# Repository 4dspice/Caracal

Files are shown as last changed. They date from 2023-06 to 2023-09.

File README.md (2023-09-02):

# Caracal

/!\ This printer is still relatively new please make sure to report any problems in  https://github.com/suslemon/Caracal/issues/1 

A fast, minimalist and modular CoreXY 3D printer that's easy to build and source parts for. All parts designed to be printed without supports. It uses 2020 extrusions and Nema 17 stepper motors. The BOM is kept as tame as possible and avoids the use of difficult to find parts. Some parts can be salvaged from other printers like an Ender 3 to further minimise costs. The printer can easily be enclosed if built using blind joints as all sides are completely flush without brackets.

Caracal was designed with modding and remixing in mind so the build is truly yours.

I printed all my parts with 0.2mm layer height, 0.4mm walls, 4 walls, 4 tops/bottoms, 30% infill (cubic) in eSun ABS+ (should be perfectly fine in PLA for non-enclosed builds) 

BOM https://docs.google.com/spreadsheets/d/1f__scBLHZBergLk1_uNWVnCNQPU6N8hWUedBBvM0iNw/edit#gid=0

YouTube Channel: https://youtube.com/@4dspice

Community Discord: https://discord.gg/pxpvCewKF5 



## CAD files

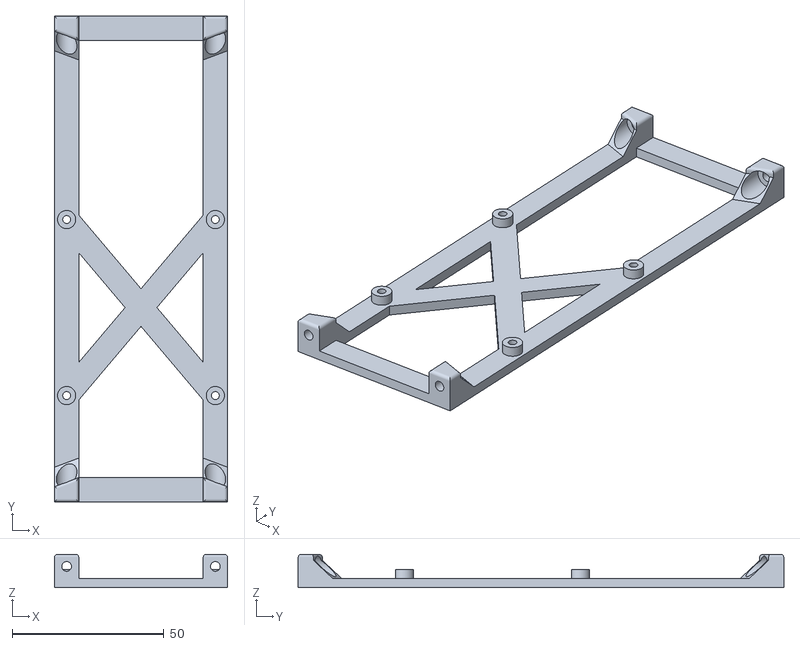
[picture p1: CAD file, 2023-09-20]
STLs/Frame/Raspberry Pi Model B Mount.stl
57.0 x 160.0 x 11.0

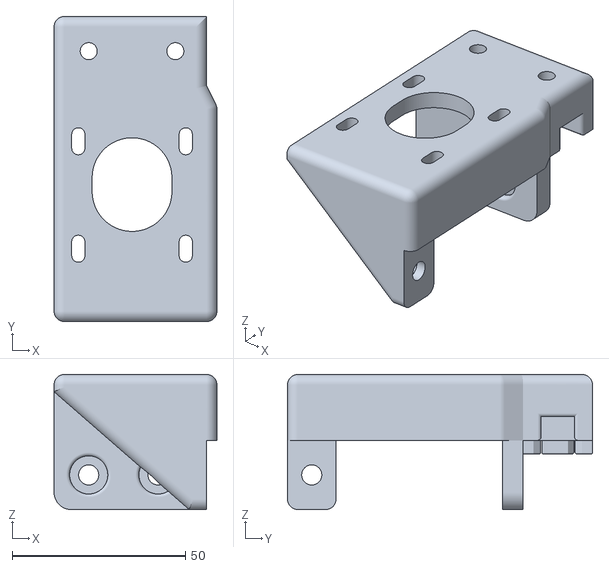
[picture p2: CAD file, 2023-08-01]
STLs/Gantry/Motor Mount - B.stl
47.0 x 88.0 x 39.0

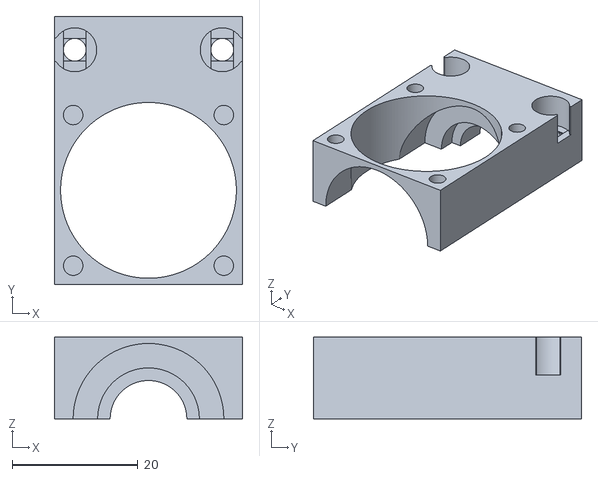
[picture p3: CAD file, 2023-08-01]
STLs/Superfang Toolhead/V6 Hotend Fan Shroud.stl
30.0 x 42.7 x 13.0

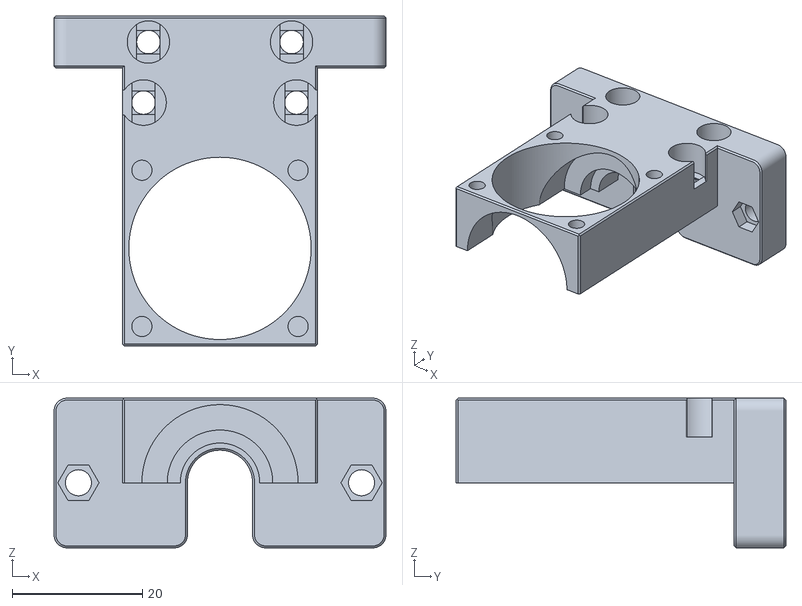
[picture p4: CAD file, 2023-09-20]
STLs/Toolhead/V6 Sherpa Mini Fan Shroud - Direct Drive.stl
51.0 x 50.7 x 23.0

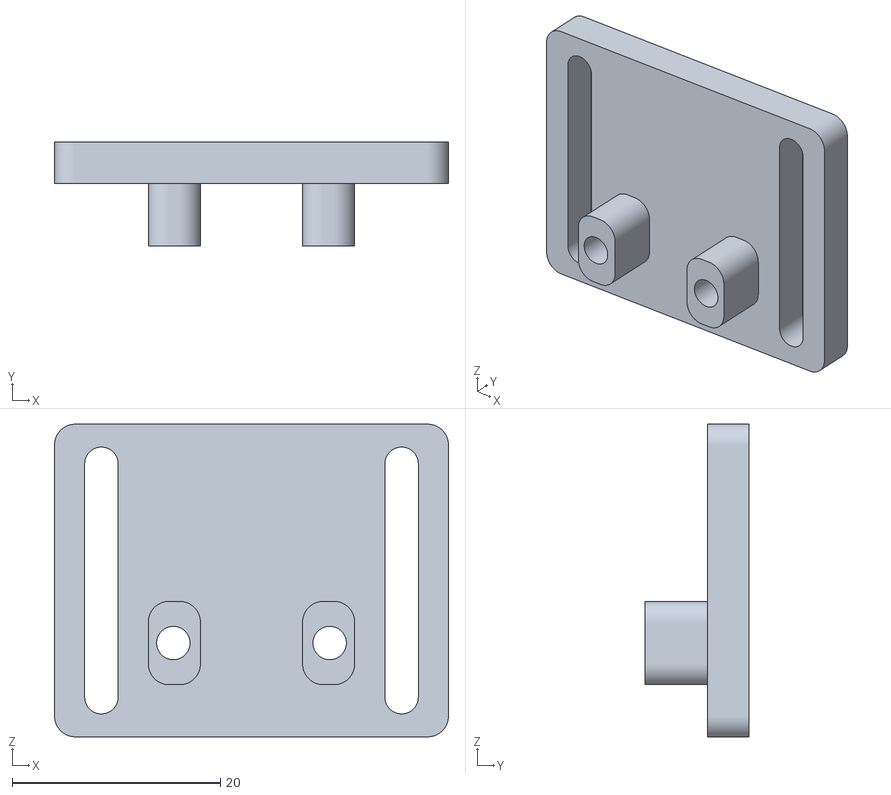
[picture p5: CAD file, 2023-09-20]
STLs/Z Assembly/Endstop Mount Creality Style.stl
37.8 x 10.0 x 30.0

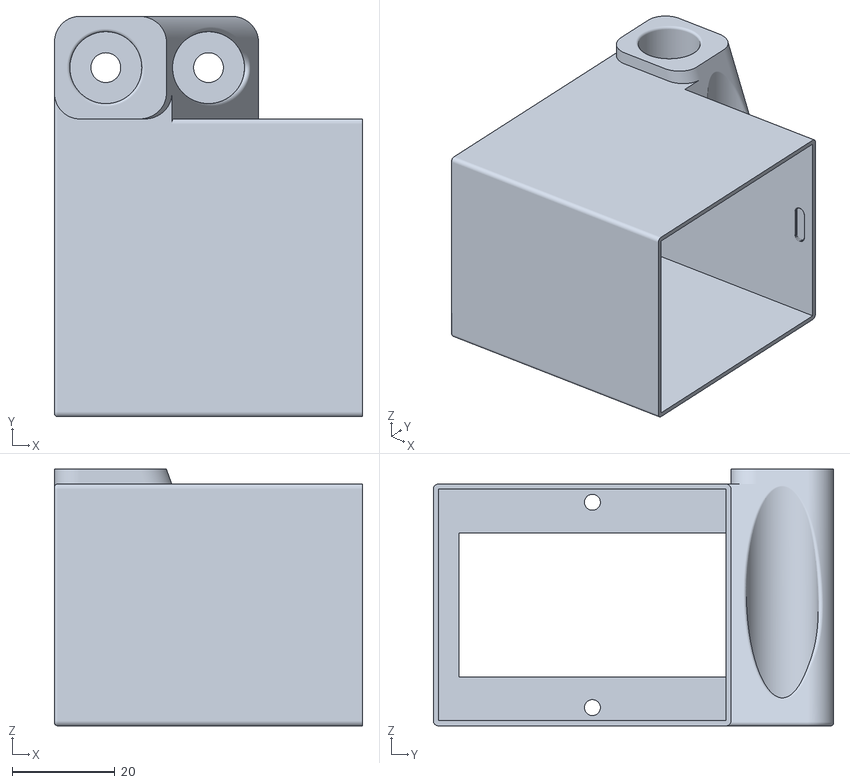
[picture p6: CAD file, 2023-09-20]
STLs/Frame/Foot Power Socket.stl
60.0 x 78.0 x 50.0

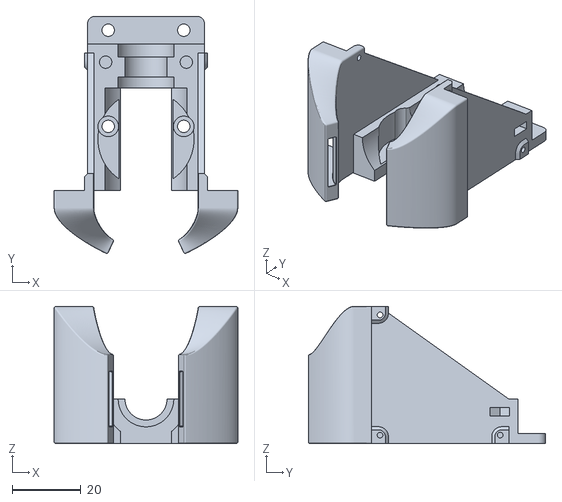
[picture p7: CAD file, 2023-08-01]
STLs/Toolhead/V6 Duct.stl
53.5 x 69.0 x 40.0

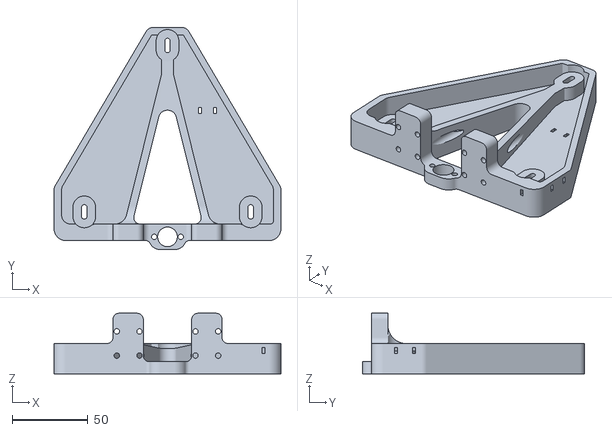
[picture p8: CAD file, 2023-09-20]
STLs/Z Assembly/Bed.stl
150.0 x 147.0 x 40.0

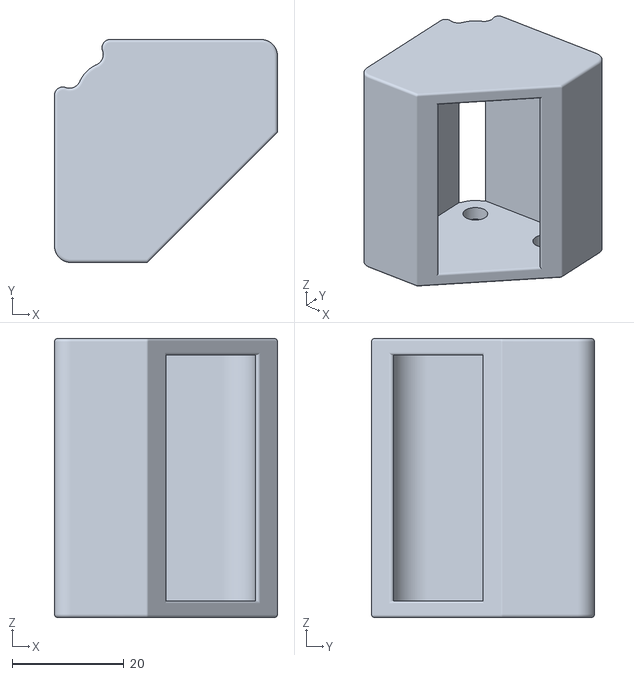
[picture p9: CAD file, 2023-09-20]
STLs/Frame/Foot Wide.stl
40.0 x 40.0 x 50.0

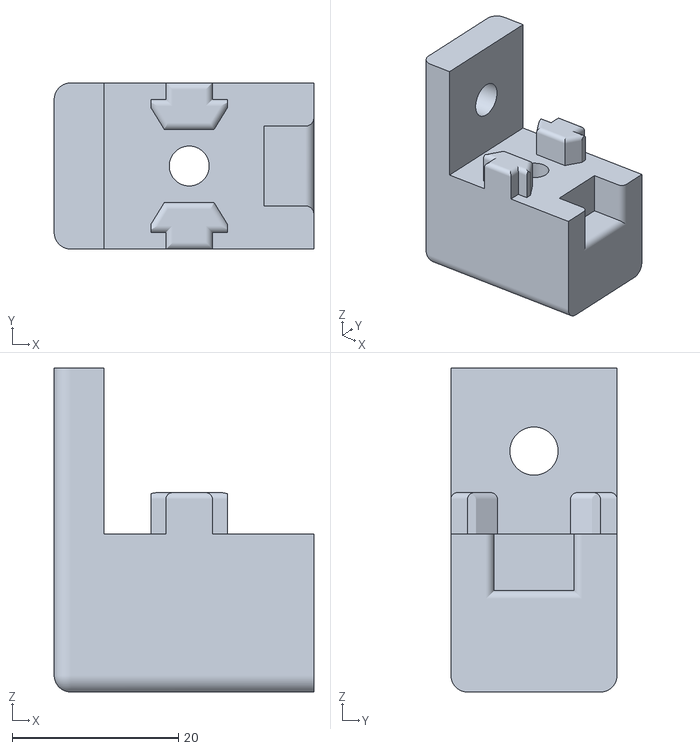
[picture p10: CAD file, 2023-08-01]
STLs/Gantry/Corner Idler.stl
31.2 x 20.0 x 39.0

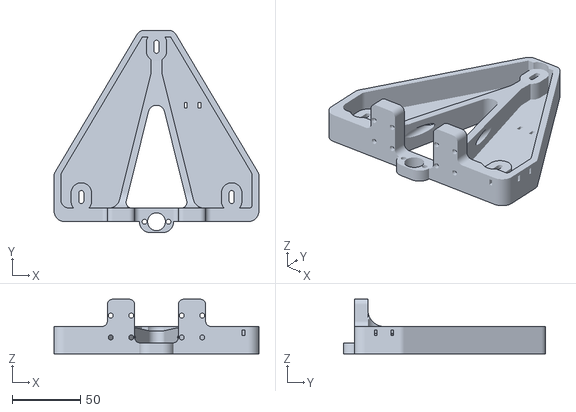
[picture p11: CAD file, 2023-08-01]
STLs/Z Assembly/Bed Mount.stl
150.0 x 148.0 x 40.0

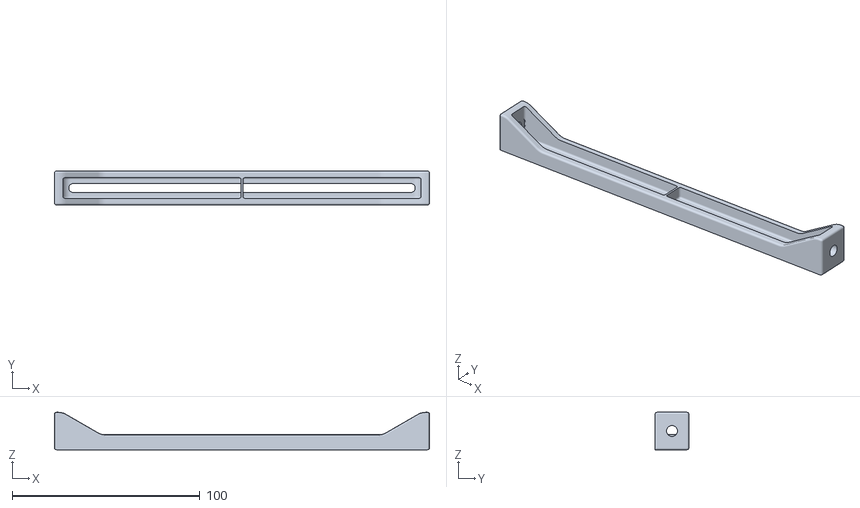
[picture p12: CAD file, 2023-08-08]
STLs/Frame/PSU Mounting Rail.stl
200.0 x 18.0 x 20.0

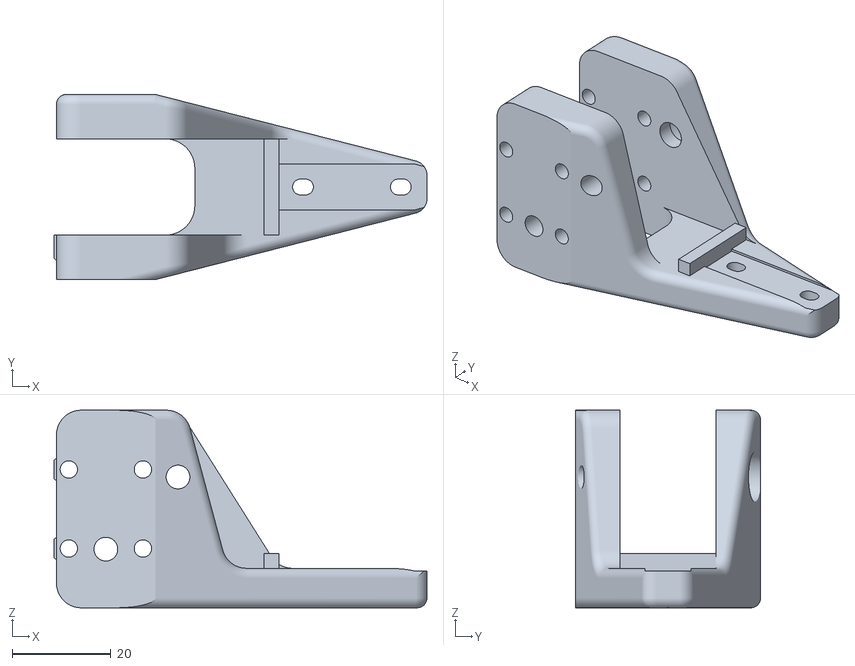
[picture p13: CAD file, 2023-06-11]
STLs/Gantry/Y Carriage - A.stl
75.5 x 37.5 x 40.0

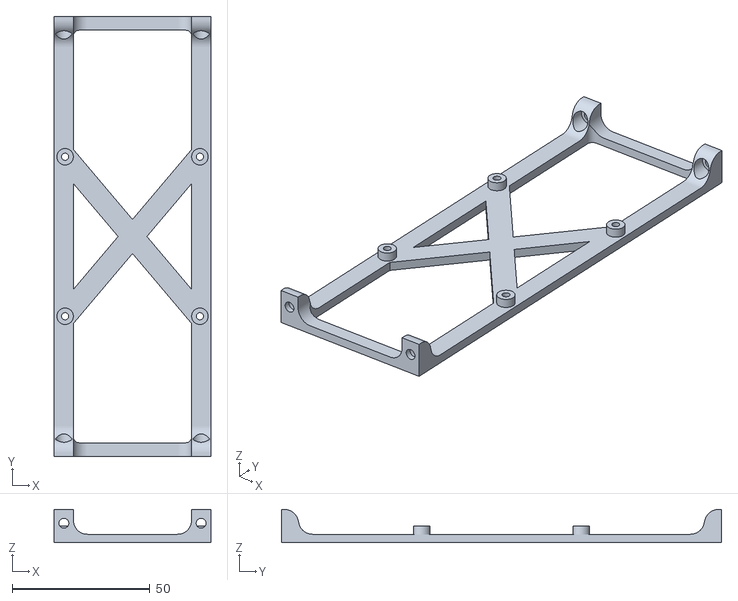
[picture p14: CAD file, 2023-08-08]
STLs/Frame/SKR Pico Mount.stl
57.0 x 160.0 x 12.0

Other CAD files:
STLs/Gantry/Motor Mount - A.stl
STLs/Gantry/Y Carriage - B.stl
STLs/Frame/Front Brace.stl
STLs/Frame/Foot.stl
STLs/Frame/Corner Bracket.stl
STLs/Frame/Internal Corner.stl

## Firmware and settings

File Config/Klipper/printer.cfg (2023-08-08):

[include mainsail.cfg]

[stepper_x]
step_pin: gpio11
dir_pin: !gpio10
enable_pin: !gpio12
microsteps: 64
rotation_distance: 40
endstop_pin: ^gpio4
endstop_pin: tmc2209_stepper_x:virtual_endstop
homing_retract_dist: 0
position_endstop: 120
position_min: -0.5
position_max: 120
homing_speed: 50

[tmc2209 stepper_x]
uart_pin: gpio9
tx_pin: gpio8
uart_address: 0
run_current: 0.8
hold_current: 0.6
#stealthchop_threshold: 999999
diag_pin: ^gpio4
driver_SGTHRS: 100

[stepper_y]
step_pin: gpio6
dir_pin: !gpio5
enable_pin: !gpio7
microsteps: 64
rotation_distance: 40
endstop_pin: ^gpio3
endstop_pin: tmc2209_stepper_y:virtual_endstop
homing_retract_dist: 0
position_endstop: 0
position_min: -0.5
position_max: 120
homing_speed: 50

[tmc2209 stepper_y]
uart_pin: gpio9
tx_pin: gpio8
uart_address: 2
run_current: 0.8
hold_current: 0.6
#stealthchop_threshold: 999999
diag_pin: ^gpio3
driver_SGTHRS: 100

[stepper_z]
step_pin: gpio19
dir_pin: gpio28
enable_pin: !gpio2
microsteps: 64
rotation_distance: 8
endstop_pin: ^gpio25
position_endstop: 120
position_min: -2
position_max: 120
homing_speed: 12

[tmc2209 stepper_z]
uart_pin: gpio9
tx_pin: gpio8
uart_address: 1
run_current: 0.580
hold_current: 0.500
#stealthchop_threshold: 999999

[extruder]
step_pin: gpio14
dir_pin: gpio13
enable_pin: !gpio15
microsteps: 64
rotation_distance: 7.710843373 # Rotation distance for BMG, adjust accordingly for other extruders
nozzle_diameter: 0.4
filament_diameter: 1.75
heater_pin: gpio23
sensor_type: ATC Semitec 104GT-2
sensor_pin: gpio27
control: pid
pid_Kp: 22.2
pid_Ki: 1.08
pid_Kd: 114
min_temp: 0
max_temp: 280
max_extrude_cross_section:2
max_extrude_only_distance: 100.0

[tmc2209 extruder]
uart_pin: gpio9
tx_pin: gpio8
uart_address: 3
run_current: 0.650
hold_current: 0.500
#stealthchop_threshold: 999999

[filament_switch_sensor runout_sensor]
switch_pin: ^gpio16
pause_on_runout: True

[heater_bed]
heater_pin: gpio21
sensor_type: EPCOS 100K B57560G104F
sensor_pin: gpio26
#control: pid
#pid_Kp: 54.027
#pid_Ki: 0.770
#pid_Kd: 948.182
min_temp: 0
max_temp: 130

[fan]
pin: gpio17

[heater_fan hotend_fan]
pin: gpio18
heater: extruder
heater_temp: 50.0


[mcu]
serial: /dev/serial/by-id/* # Change this line with your MCU id 
restart_method: command

[printer]
kinematics: corexy
max_velocity: 500
max_accel: 8000 # Conservative default 
max_z_velocity: 50
max_z_accel: 30

[bed_screws]
screw1: 5, 5
screw2: 115, 5
screw3: 60, 115

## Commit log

2023-07-11 Upload bed mount
    [Corner Raiser.stl]
2023-08-01 final files added, printing state
    [Bed Mount.stl, Corner Bracket.stl, Corner Idler.stl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]
2023-08-08 update stls
    [Bed Mount.stl, Endstop Mount Creality Style.stl, PSU Mounting Rail.stl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]
